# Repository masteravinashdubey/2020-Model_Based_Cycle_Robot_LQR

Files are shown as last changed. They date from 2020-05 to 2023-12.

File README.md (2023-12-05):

# Model Based Robot Designing

- This project is part of e-YSIP(E-yantra Summer Internship Programme), 2020.
- Project Mentors: Avinash Dubey, Avijit Pandey
- Project Interns: Shreya Rastogi, Jai Garg, Chinmay Palaye
- The objective of this project is to understand and implement LQR based robot modelling.
- In this Project, we'll learn to design control strategies & model various robots.
- We will simulate different systems and robots based on the chosen model.
- We will also be building learning modules and experiments for better understanding of topics.
- The project has been divided into weeks. The work done in each week is contained in that weeks folder.
- Daily reports folder contains daily reports till day 6 for the team. After that the interns updated their personal reports.
- Meeting reports folder contains the minutes of the meetings with the mentors.
- Project progress report folder tracks the progress of the project so far.
- Weekly reports folder contains the weekly reports.
- The video link is : <a href="https://www.youtube.com/watch?v=THvqfcC5Y-I&list=PLK0jpMYIBd6B1-mDQZwADi5OlnOiK6k9m&index=19"> LQR based Cycle Robot </a>

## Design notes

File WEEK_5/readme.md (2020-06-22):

# Optimal Control Strategy
We were supposed to design 4 experiments/explanatory documents for this week.
1. Defining LQR Control. Impact of Q and R matrix (LQR_CONTROL)
2. Implementing LQR Control in Octave (LQR_control_Octave)
3. Implementing the Feedback in Arduino. Tuning the Parameters. (sensors_and_tuning)
4. Strategy for Navigation Via Remote Control. Debugging the System.

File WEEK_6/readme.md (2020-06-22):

# Hardware Implementation of Cycle Bot

This folder contains all the codes which have been used in Cyclebot Implementation.
- cycle_bot_arduino : main code of the bot
- timerInterrupt : code for the two timers being used
- Cycle__bot.m : Octave code for K matrix calculation using dlqr()
- mpu caliberation.txt : offset calculation of mpu
- serialTest

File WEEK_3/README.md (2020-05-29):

# Robot Hardware
- 3 experiments to be designed.
  1. 3D Modelling in VREP.
  2. Collecting data using GY87 and filtering it, comparison between various filters.
  3. Interfacing XBee with Arduino.
- 2 videos to be made
  1. Factors to consider while choosing hardware
  2. Do's and Don'ts of robot hardware

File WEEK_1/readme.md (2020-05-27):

# Simulation of Cycle Bot
- This week's work was divided into 3 tasks.
  1. Task 1: simulation of a Reaction wheel balanced inverted pendulum on a hinge.
  2. Task 2: simulation of a Reaction wheel balanced inverted pendulum on a pivot.
  3. Task 3: simulation of a Cyclebot.

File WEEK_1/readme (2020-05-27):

Simulation of Cycle Bot
- This week's work was divided into 3 tasks.
- Task 1 was the simulation of a Reaction wheel balanced inverted pendulum on a hinge.
- Task 2 was the simulation of a Reaction wheel balanced inverted pendulum on a pivot.
- Task 3 was the simulation of Cyclebot.

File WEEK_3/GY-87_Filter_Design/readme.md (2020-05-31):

# GY-87_Filter_Design
- This folder contains the experiment files for the topic GY-87 and filter design.
- There is an experiment problem file.(Experiment.pdf)
- There is an experiment solution file.(Filter_design_answers.pdf)
- The .tex files for both are also present.
- The folder Experiment_Octave_Files consists of all the files for the octave part of this experiment.

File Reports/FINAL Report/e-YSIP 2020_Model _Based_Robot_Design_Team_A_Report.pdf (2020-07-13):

## eYSIP 2020

### Model Based Robot Design

### Project ID 17

### Chinmay Palaye Jai Garg Shreya Rastogi Avinash Dubey Avijit Pandey Duration of Internship: 08/05/2020 − 27/06/2020

2020, e-Yantra Publication

# Model Based Robot Design

## Abstract

A self-balancing bicycle robot based on the concept of an inverted pendulum is an unstable and nonlinear system. This system balances using a reaction wheel, also known as inertia wheel. Behaviour of this system is studied by deriving a mathematical model of the system using Euler Lagrange method. This model is used to balance the cycle robot using LQR control method. To apply LQR, system is first linearized about the equilibrium points using Jacobian method. This model was first simulated in the simulation software CoppeliaSim (VREP). A physical cycle robot was designed in Fusion360 software, manufactured, and balanced. Project Overview video (https://www.youtube.com/watch?v=MRSbph5AvGU&t=7s)

### Completion status

The project has been completed successfully. Learning Modules were created for various topics of Control systems and LQR controller. Cyclebot was simulated in CoppeliaSim and also implemented using hardware.

## 1.1 Hardware parts

- GY87 10DOF 3axis accelerometer, gyroscope, magnetometer: Datasheet
- XBee Module: Datasheet
- Arduino Mega2560: Datasheet
- L298 motor driver: Datasheet
- GS5515MG Servo Motor: Datasheet

1

1.2. SOFTWARE USED

## 1.2 Software used

- CoppeliaSim:

– Version 4.0.0

– Download Link (https://www.coppeliarobotics.com/downloads)

– User Manual (https://www.coppeliarobotics.com/helpFiles/)

- GNU Octave:

– version 5.1.0.0

– Download Link (https://www.gnu.org/software/octave/download.html)

– Installation Steps (https://wp.stolaf.edu/it/installing-gnu-octave-on-windows/)

- Fusion 360TM:

– Version 2.0.8156

– Download Link (https://www.autodesk.com/products/fusion-360/free-trial)

– Installation Steps (https://knowledge.autodesk.com/support/fusion-360/troubleshooting/caas/sfdcarticles/sfdcarticles/How-does-Fusion-360-get-installed.html)

- Arduino IDE:

– Version 1.8.39.0

– Download Link (https://www.arduino.cc/en/main/software)

– Installation Steps (https://www.tutorialspoint.com/arduino/arduino_installation.htm)

## 1.3 Assembly of hardware

Circuit diagram and Steps of assembly of hardware with pictures for each step.

### Circuit Diagram

Figure 1.1 shows the circuit diagram of Cycle Bot.

www.e-yantra.org | 2

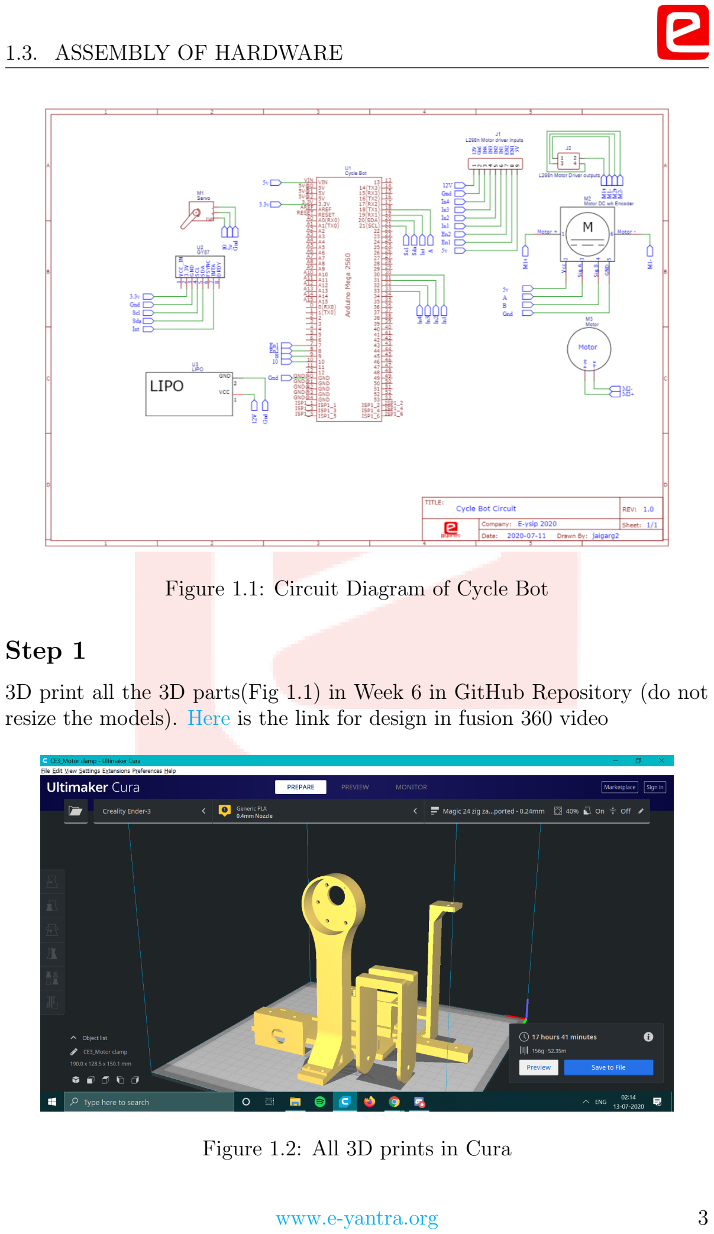
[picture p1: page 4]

1.3. ASSEMBLY OF HARDWARE

Figure 1.1: Circuit Diagram of Cycle Bot

### Step 1

3D print all the 3D parts(Fig 1.1) in Week 6 in GitHub Repository (do not resize the models). Here (https://www.youtube.com/watch?v=4ax1faUiTyk) is the link for design in fusion 360 video

Figure 1.2: All 3D prints in Cura

www.e-yantra.org | 3

1.3. ASSEMBLY OF HARDWARE

### Step 2

Attach Servo case and handle to the servo motor

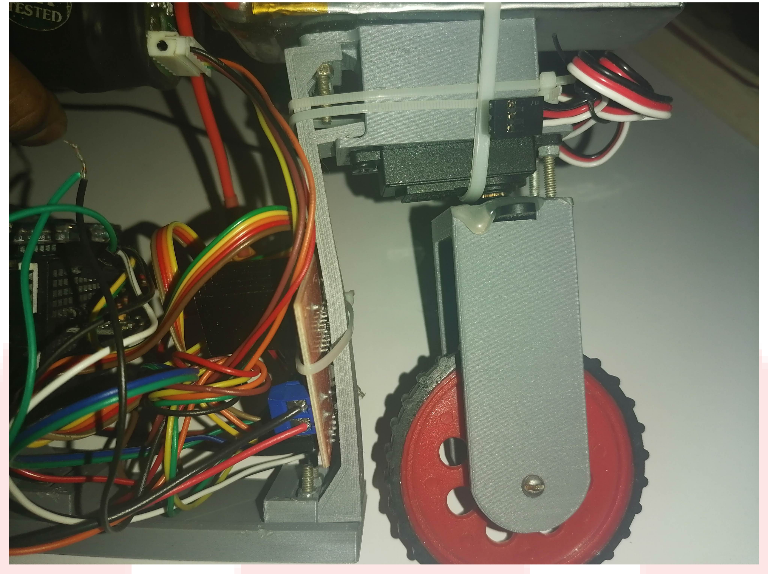
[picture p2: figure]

Figure 1.3: Front Assembly

### Step 3

Attach middle slab and base using screws.

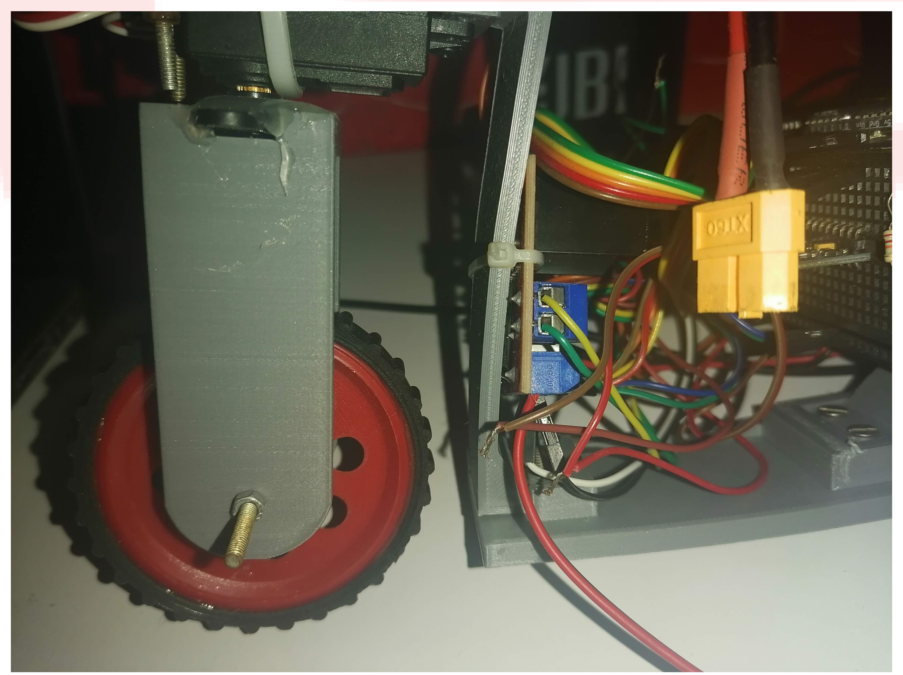
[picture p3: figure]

Figure 1.4: Base Connection

www.e-yantra.org | 4

1.3. ASSEMBLY OF HARDWARE

### Step 4

Connect reaction wheel motor and base motor to reaction wheel stand and motor clamp respectively and then attach both on the base using screws(Fix reaction wheel tightly).

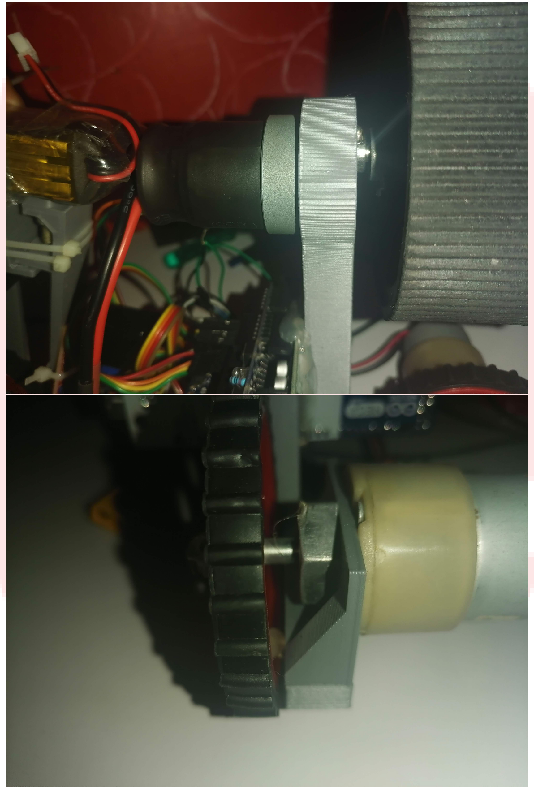
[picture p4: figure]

Figure 1.5: Reaction Wheel and Motor Clamp

www.e-yantra.org | 5

1.4. SOFTWARE AND CODE

### Step 5

Then Connect all the electronic Components according to the circuit diagram.

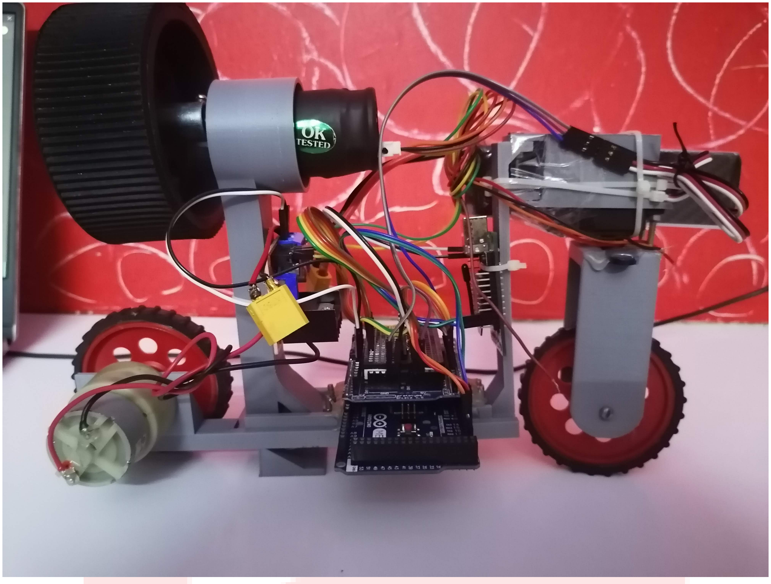
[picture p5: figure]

Figure 1.6: Fully assembled bot

## 1.4 Software and Code

GitHub link (https://github.com/masteravinashdubey/Model_Based_Robot_LQR/tree/master/WEEK_6) for the repository of code
Brief explanation of various parts of code:
- Main loop.ino: The main code where the rest of the header files and functions have been called.
- motor.h: The file where the functions and working of the motors and related calculations take place.
- controller lqr.h: The header file containing the controller of the system. The LQR controller has been implemented in this.
- DMP.h: This code gives the readings from the MPU6050 i.e. the roll and the pitch of the system.
www.e-yantra.org | 6

1.5. USE AND DEMO
- mpu.h: This code gives us the readings from the MPU6050 using filters.
- torque model.m: This is the octave code which fives us the value of the gain matrix i.e. K matrix for our system.
- xbee.h: This is for the communication between our bot and the remote via Zigbeee communication.

## 1.5 Use and Demo

Final Setup Image

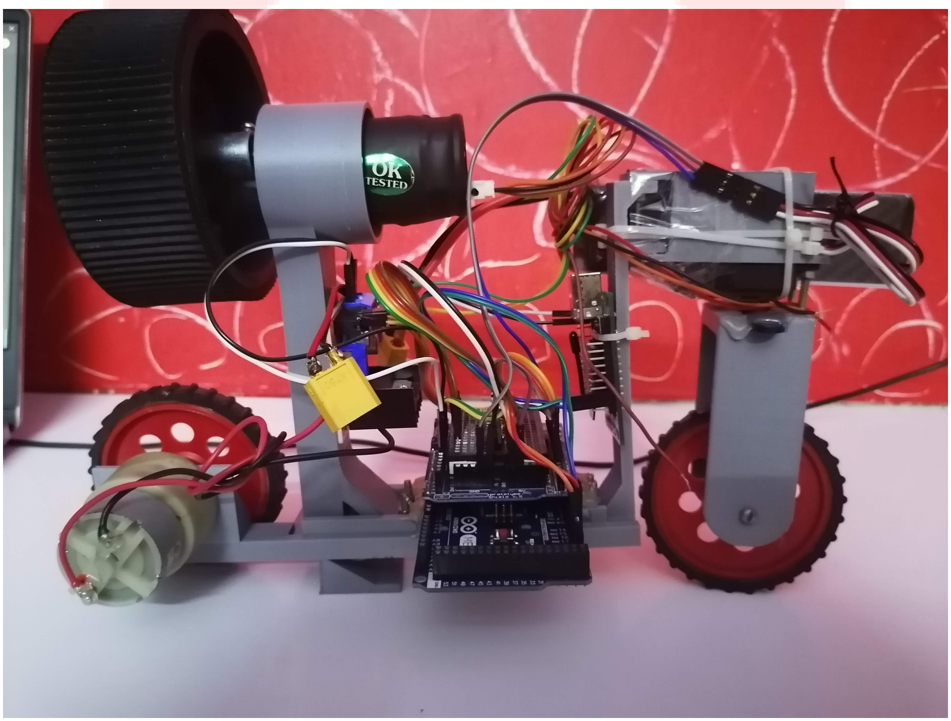
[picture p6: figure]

Figure 1.7: Fully assembled bot

Youtube Link (https://www.youtube.com/watch?v=o6guLBFLpi8) of demonstration video

## 1.6 Future Work

Presently we have managed to balance the cyclebot for a very short duration i.e. a few seconds. In the future the first thing to be implemented would be it’s successful balancing. Then more work can be done regarding it’s

www.e-yantra.org | 7

1.7. BUG REPORT AND CHALLENGES

movement. The cyclebot should be able to move forward, take turns, climb an inclined plane etc. in the future projects.

## 1.7 Bug report and Challenges

Failure or challenges faced during project:

- The hardware wasn’t available for making the cyclebot so we had to take help of a 3D printer.
- The implementation of LQR controller to balance the cyclebot was a huge challenge.
- Main challenge faced was in balancing the cyclebot.
- Usage of timers in the code was slightly tricky as well.
www.e-yantra.org | 8

# Bibliography

[1] Kiattisin Kanjanawanishkul, LQR and MPC controller design and comparison for a stationary self-balancing bicycle robot with a reaction wheel, 2015.
[2] Adam Owczarkowski, Dariusz Horla and Joanna Zietkiewicz, Introduction of feedback linearization to robust LQR and LQI control – Analysis of results from an unmanned bicycle robot with reaction wheel, 2019.
[3] Jepsen, Frank; Søborg, Anders; Pedersen, Anders R.; Yang, Zhenyu, Development and Control of an Inverted Pendulum Driven by a Reaction Wheel, 2009.
[4] Yon Yaw Lim, Choon Lih Hoo, and Yen Myan Felicia Wong, Stabilising an Inverted Pendulum with PID Controller, 2018.

9

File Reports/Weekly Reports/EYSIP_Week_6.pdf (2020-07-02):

# EYSIP 2020 Weekly Report

### Saturday, 21.06.2020

─

# Cycle BOT using LQR

## Team 1 (LQR)

Shreya Rastogi
Jai Garg
Chinmay Palaye

## Important Points

Hardware implementation of Cyclebot.

- cycle_bot_arduino : main code of the bot
- timerInterrupt : code for the two timers being used
- Cycle__bot.m : Octave code for K matrix calculation using dlqr()
- mpu caliberation.txt : offset calculation of mpu
- serialTest

## Relevant Links:

- All the work has been updated in the GitHub repository in the WEEK_6 folder.

Link (https://github.com/masteravinashdubey/Model_Based_Robot_LQR/tree/master/WEEK_6)

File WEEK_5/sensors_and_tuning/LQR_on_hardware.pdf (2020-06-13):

## Robot Design Robot Design using LQR

### Choice of Sensors and Tuning

### 1 Choice of Sensors:

The input given to the system, u = −Kx, depends on the gain matrix K, and the instantaneous values of all the state variables. Gain matrix can be calculated by using A and B matrices of the system, and setting appropriate values in Q and R matrices. On the actual robot, instantaneous values of all state variables are needed in order to calculate the input to the actuators. To get those values, various sensors are needed. Type of sensor depends on the type of value needed, and the structure of robot.

- Angular position of a joint: A rotary encoder can be used to get this. If angular velocity is needed, This value can be differentiated with respect to time using timer interrupts.

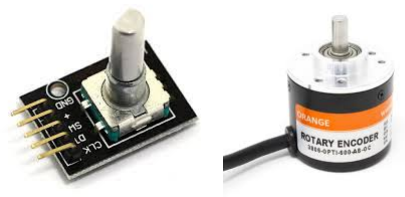
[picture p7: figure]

(a) (b)

Figure 1: Rotary Encoders

- Roll, pitch or yaw of a body: IMUs like accelerometer, magnetometer, etc. can be used. For rate of change, gyroscope can be used.

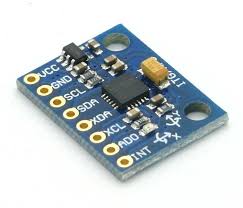
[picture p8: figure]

Figure 2: MPU6050: Accelerometer+Gyroscope

1

- Linear Position of joint: a linear encoder(e.g. LVDT) can be used. Some mechanism like rack and pinion can be used to make the use of rotary encoder to get the position. The differentiation technique can be used to get linear velocity as well.

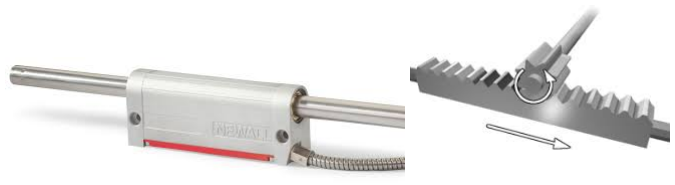
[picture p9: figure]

(a) Linear Encoder | (b) Rack and Pinion Mechanism

Figure 3: Linear Position Sensors

- Displacement of the robot: Rotary encoders can be attached to the robot with dummy wheels. Angular position of the encoder will be directly proportional to the displacement of robot. If walls are available for reference, distance sensors can be used to determine the distance for robot from the walls.

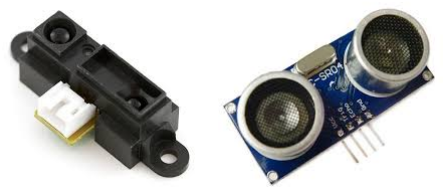
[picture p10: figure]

(a) Optical | (b) Sound based

Figure 4: Distance Sensors

Readings from all these sensors might have to be processed to match the units and conventions used while deriving the model.

2

### 2 Tuning of Q and R matrices:

To decide the gain matrix, Q and R matrices need to be adjusted such that the system is stable, and performance is optimal. Higher Q values mean that more preference is given to that state variable. When Q of some state variable is increased, gain values will change in such a way that the system will react more on change in the value of that variable. While tuning, observe the performance of the system and increase or decrease the weights accordingly.

3

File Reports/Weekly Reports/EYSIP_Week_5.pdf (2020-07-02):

# EYSIP 2020 Weekly Report

### Saturday, 13.06.2020

─

# Cycle BOT using LQR

## Team 1 (LQR)

Shreya Rastogi
Jai Garg
Chinmay Palaye

## Important Points

We designed 4 experiments/explanatory documents for this week.

1. Defining LQR Control. Impact of Q and R matrix.
2. Implementing LQR Control in Octave.
3. Implementing the Feedback in Arduino. Tuning the Parameters.
4. Strategy for Navigation Via Remote Control. Debugging the System.

## Relevant Links:

- All the work has been updated in the GitHub repository in the WEEK_5 folder.

Link (https://github.com/masteravinashdubey/Model_Based_Robot_LQR/tree/master/Week_5)

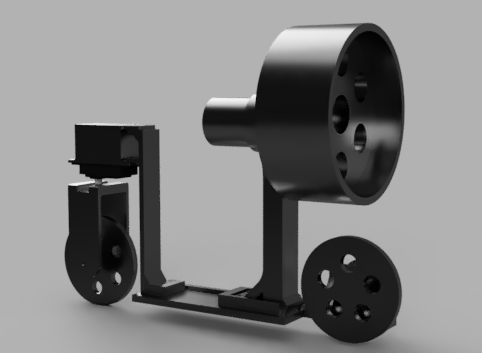
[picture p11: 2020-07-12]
WEEK_6/Bot design/Bot_3D_Design.png

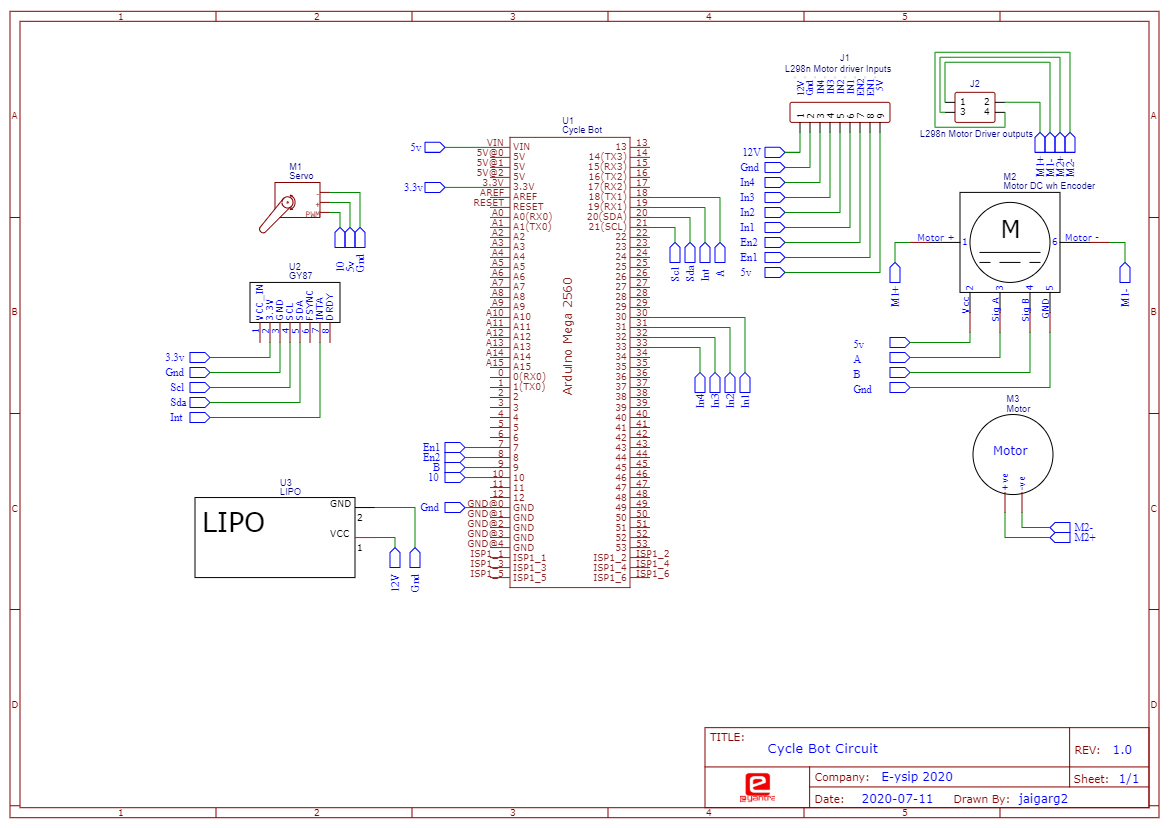
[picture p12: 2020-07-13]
WEEK_6/Schematic_E-YSIP 2020 Cycle Bot_2020-07-12_00-36-34.png

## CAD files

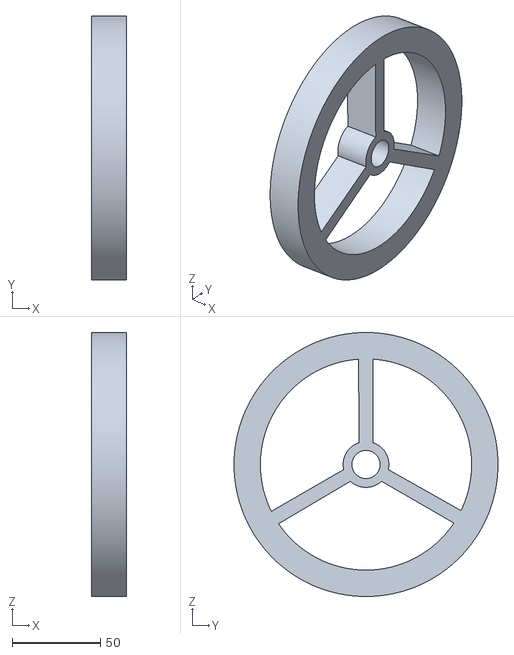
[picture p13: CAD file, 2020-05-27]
WEEK_1/Task_1/Fusion 360 files/Wheel.stl
20.0 x 150.0 x 150.0

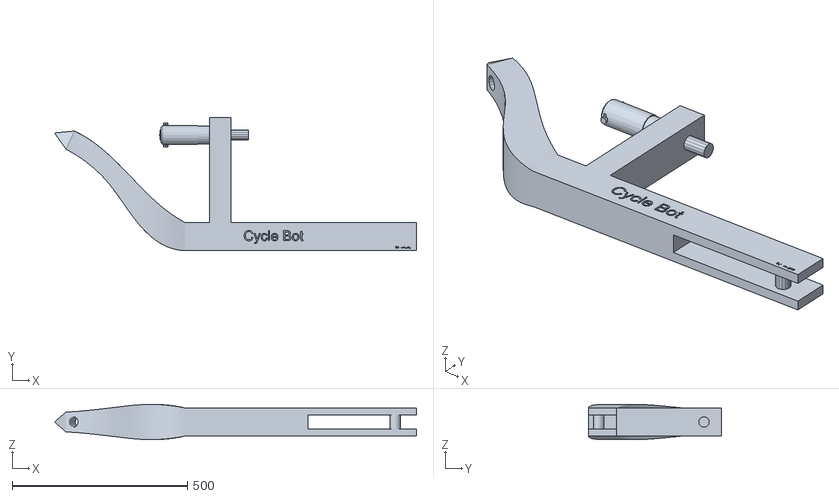
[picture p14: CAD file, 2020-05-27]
WEEK_1/Task_3/Design in Fusion 360/.stl_files/Cycle Body.stl
1032.6 x 380.0 x 100.1

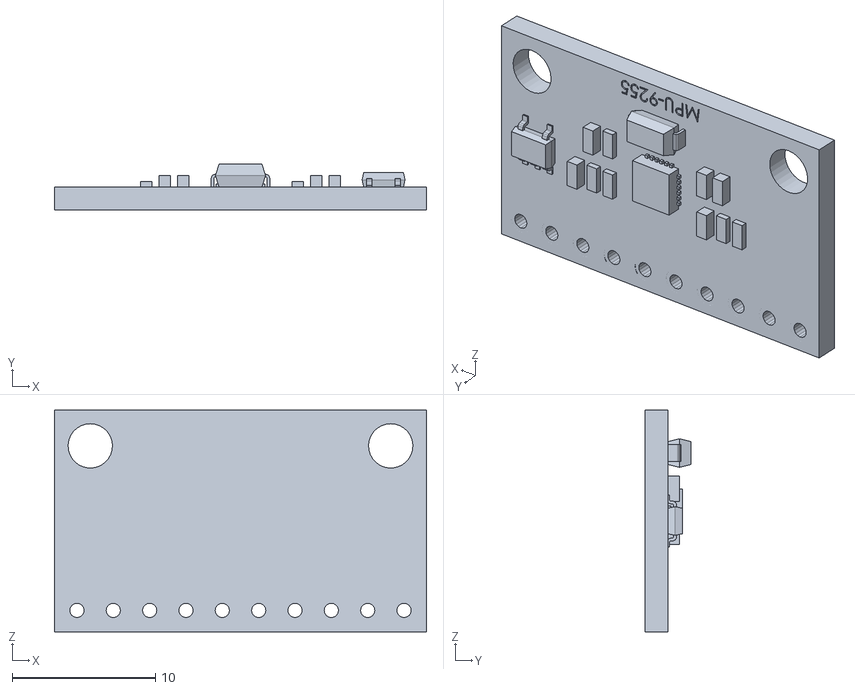
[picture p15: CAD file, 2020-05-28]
WEEK_3/Experiment 1/Fusion 360/Files/Gy-87.stl
26.0 x 3.20 x 15.5

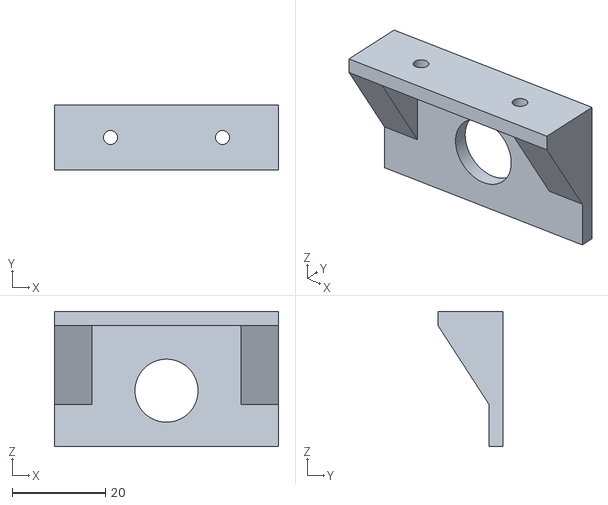
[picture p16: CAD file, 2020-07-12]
WEEK_6/Bot design/3D print Files/Motor clamp.stl
48.0 x 14.0 x 29.0

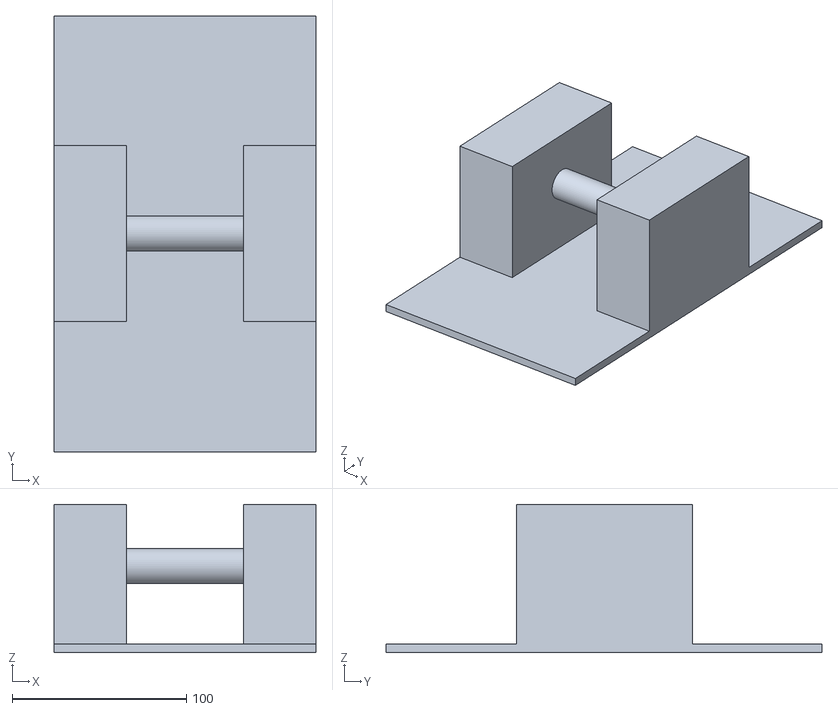
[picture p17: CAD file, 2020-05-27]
WEEK_1/Task_1/Fusion 360 files/Simple Base.stl
150.0 x 250.0 x 85.0

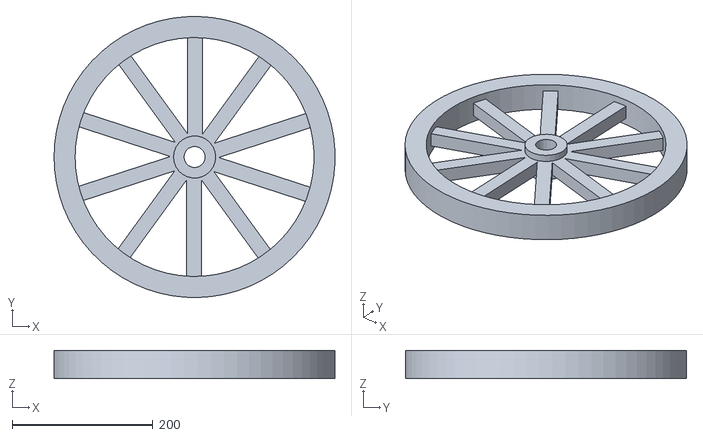
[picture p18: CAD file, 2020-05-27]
WEEK_1/Task_3/Design in Fusion 360/.stl_files/Wheel.stl
399.8 x 399.9 x 40.0

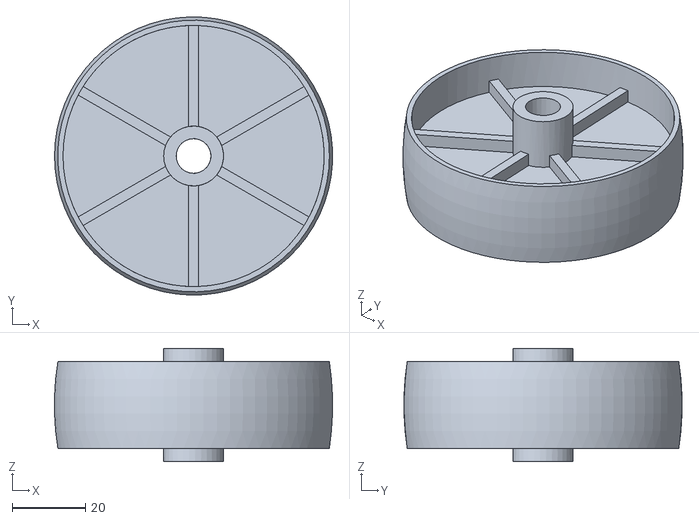
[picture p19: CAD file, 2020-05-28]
WEEK_3/Experiment 1/Fusion 360/Files/Wheel.stl
76.1 x 76.1 x 31.0

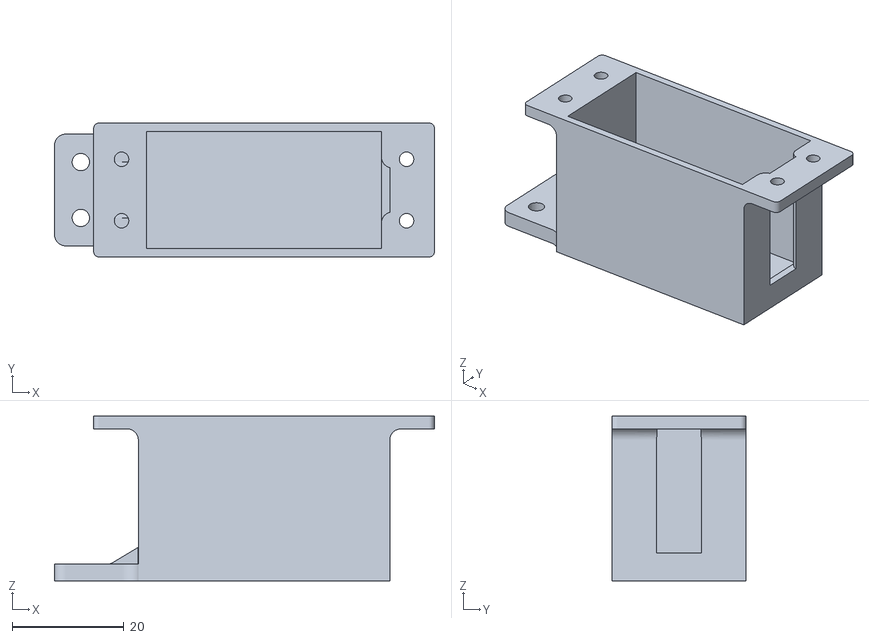
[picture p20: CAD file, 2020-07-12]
WEEK_6/Bot design/3D print Files/Servo case V2.stl
68.0 x 24.0 x 29.5

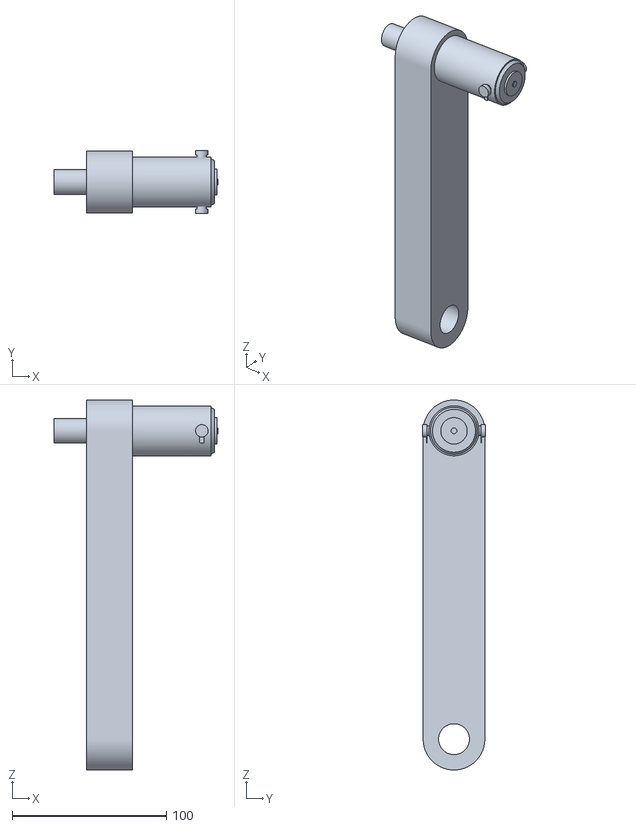
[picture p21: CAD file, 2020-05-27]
WEEK_1/Task_1/Fusion 360 files/Pendulum.stl
106.3 x 41.1 x 240.0

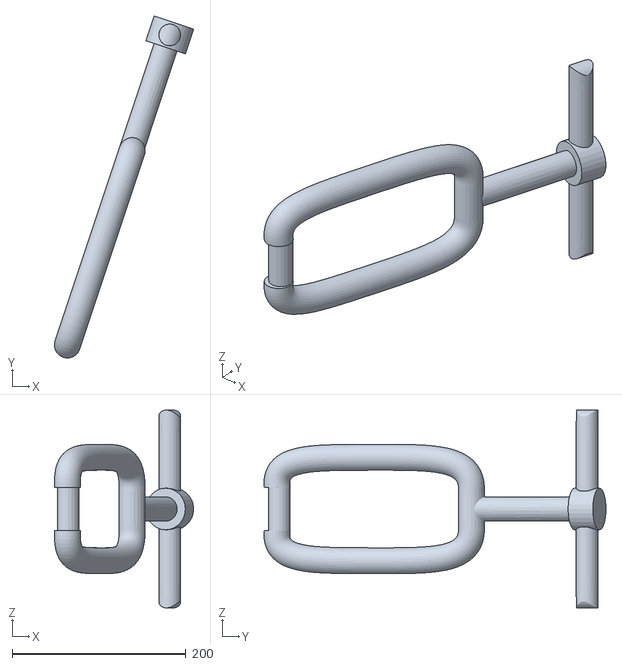
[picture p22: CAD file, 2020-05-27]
WEEK_1/Task_3/Design in Fusion 360/.stl_files/Handle.stl
160.4 x 394.1 x 228.0

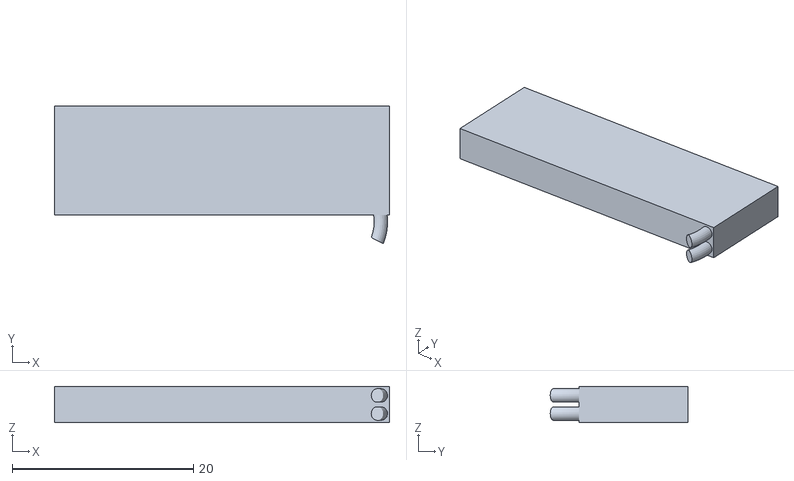
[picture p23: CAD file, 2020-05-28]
WEEK_3/Experiment 1/Fusion 360/Files/LiPo_Battery.stl
37.0 x 15.2 x 4.00

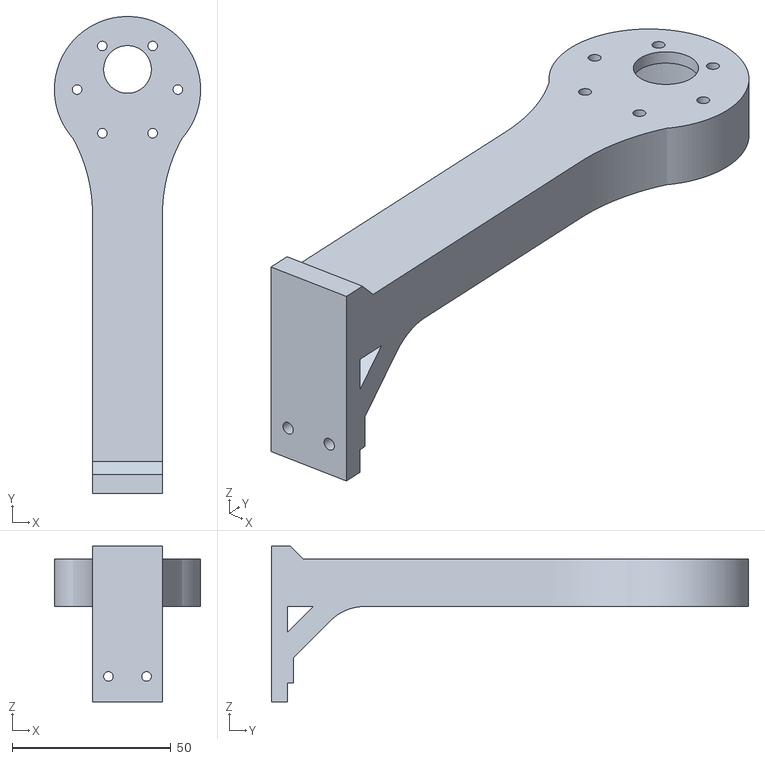
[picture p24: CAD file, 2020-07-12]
WEEK_6/Bot design/3D print Files/Reaction wheel v3.stl
46.0 x 150.1 x 49.0

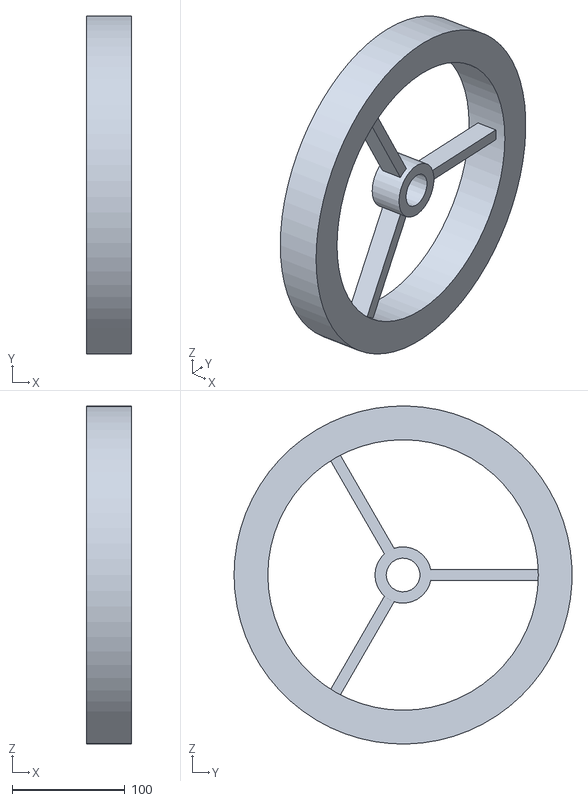
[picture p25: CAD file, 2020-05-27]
WEEK_1/Task_3/Design in Fusion 360/.stl_files/Reaction wheel.stl
40.0 x 299.8 x 299.9

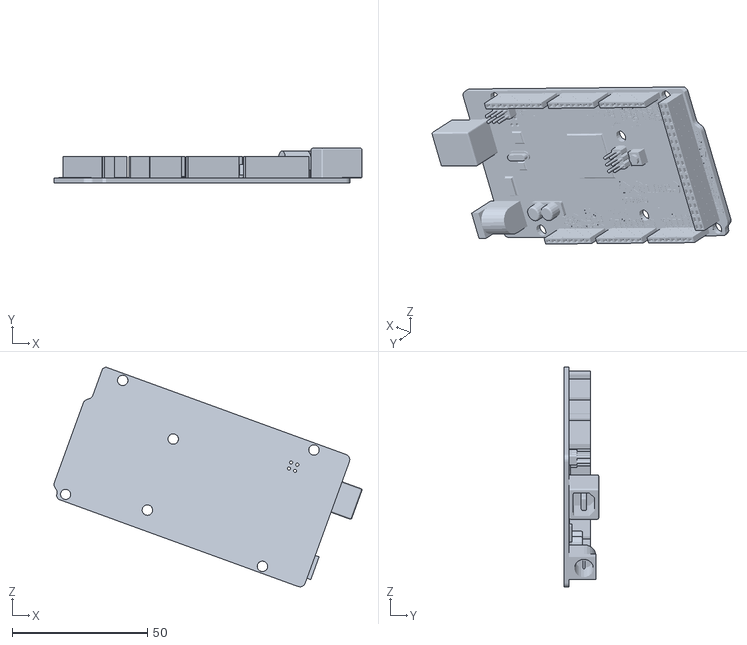
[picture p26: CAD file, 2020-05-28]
WEEK_3/Experiment 1/Fusion 360/Files/ARDUINO MEGA.stl
114.0 x 12.8 x 81.4

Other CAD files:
WEEK_6/Bot design/3D print Files/Middle slab.stl
WEEK_1/Task_3/Design in Fusion 360/.stl_files/Cycle Bot design v2.stl
WEEK_3/Experiment 1/Fusion 360/Files/Body.stl
WEEK_6/Bot design/3D print Files/Base V2.stl
WEEK_3/Experiment 1/Fusion 360/Files/DC Motor.stl
WEEK_3/Experiment 1/Fusion 360/Files/L298N Motor Driver.stl
WEEK_3/Experiment 1/Fusion 360/Files/Motor Clamp.stl
WEEK_3/Experiment 1/Fusion 360/Files/XBee.stl
WEEK_6/Bot design/3D print Files/Servo Steering for cycle bot v1.stl

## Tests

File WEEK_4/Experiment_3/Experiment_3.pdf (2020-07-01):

E-Yantra Summer Internship

PID:17 | 26th June, 2020

# State-Space Model and Controllability

### 1 Aim

Finding out the Parametric State-Space Model. Substituting practical values and checking for

controllability of the system.

### 2 Problem

- Consider the system of a Cyclebot. In the previous experiment we derived the state space

model of the system. The input to this system was an input torque. Find the model in

terms of an input voltage i.e. find the relation between voltage and torque and find the

resultant model of the system.

- The hardware or the cyclebot that you have built. Find it’s values, for example mass,

moment of inertia, torque etc. Substituting these values in the A and B matrices, check

whether the actual system is controllabale or not.

### 3 Solution

Let [θ, ˙θ, φ, φ˙
]

T be the state variables of the system

where:

θ: deflection of the pendulum from the vertical ˙θ: angular velocity of the pendulum

φ: angle of the reaction wheel
φ˙
: angular velocity of the reaction wheel

∴ State Space Representation of the system

x˙ = Ax + Bu | (1)

˙θ

¨θ

φ˙

φ¨

=

0 1 0 0

b
a

0 0 0

0 0 0 1
−

b
a

0 0 0

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
(a+I2)
aI2

Tr

where

a = (m1L

2
1 + m2L

2
2 + I1) | (2)
b = (m1L1 + m2L2)g | (3)

To control the speed of the reaction wheel to the desired one, the following mathematical model

is the physical behavior of the motor with a gear system:

V = Lm

di
dt + Rmi + Keωm

Tm = Kti

Tr = NgTm

where:

- V : motor supply voltage
- Ke : motor back emf constant
- ωm : motor angular speed
- Lm : armature coil inductance
- Rm : armature coil resistance
- i : armature current
- Tm : motor generated torque
- Kt

: motor torque constant

- Ng : gear ratio

The term of inductance can be neglected since, in general, the motor inductance value is much less than the motor resistance value (Lm«Rm). By using the relationship between the motor and the reaction wheel, i. e., φ˙ = ωr, ωm = Ngωr, where ωr is reaction wheel angular speed, the

motor supply voltage can be found in terms of the reaction wheel angle as follows:

Tr = NgKt

V − KeNgφ˙

Rm

The Model:

˙θ

¨θ

φ˙

φ¨

=

0 | 1 0 | 0
a21 | 0 0 a24
0 | 0 0 | 1
a41 | 0 0 a44

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
where:

a21 =

b
a

, a24 =

KtKeNg

2
aRm

, a41 = −

b
a

, a44 = −

(a+I2)
aI2

KtKeNg

2
Rm

, b2 = −

KtNg
aRm

, b4 =

(a+I2)
aI2

KtNg
Rm

### Parameters of Our Cyclebot

Parameters | Values
Distance from pivot to COM of Body (L1) | 76.83mm
Distance from pivot to COM of Reaction Wheel (L2) | 148.53mm
Mass of Bicycle (M1) | 763g
Mass of Reaction Wheel (M2) | 357g
MOI of Body about COM (I1) | 2.1x10⁶ gmm²
MOI of Reaction wheel about COM (I2) | 8.2x10⁵ gmm²
Motor Resistance (Rm) | 13.3 Ω
Motor Torque Constant (Kt) | 2.77x10⁻²Nm/A
Motor Back EMF Constant (Ke) | 1.27x10⁻²V s/rad
Motor gear ratio (Ng) | 1:30

The model obtained by substituting these values is:

˙θ

¨θ

φ˙

φ¨

=

0 | 1 0 | 0
75.64 | 0 0 | 1.6482
0 | 0 0 | 1

−75.64 0 0 −2.0678e − 05

θ
˙θ

φ
φ˙

+

0

−4.3151

0

80.512

V

Using the above A and B matrices and the controllability matrix of the system

CO = [B, AB, A²B, A³B]

we check whether this system is controllable or not. Using the ctrb(A,B) function in octave,

we find the controllability matrix of this system. Then using the rank(CO) function we get

rank = 4, which proves that this system is controllable.

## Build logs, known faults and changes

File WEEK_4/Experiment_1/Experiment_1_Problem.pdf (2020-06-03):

E-Yantra Summer Internship

PID:17 | 3rd May, 2020

# Kinetic and Potential energy of a system

### 1 Aim

To find out the Kinetic energy and Potential energy of a system. Using these two quantities,

find out the Lagrangian of the system and the Euler Lagrange equation.

### 2 Problem

Consider the system of a Cyclebot. A Cyclebot is a robot having two wheels and balanced by

the help of a reaction wheel. It resembles a self balancing bot system. For this system, find out

the Kinetic energy,the Potential energy and then subsequently go on to find it’s Lagrangian and

the Euler Lagrange equation.

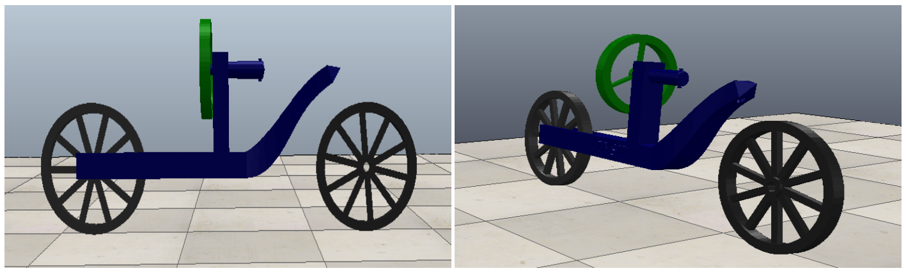
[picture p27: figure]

List of symbols:

- m1 : mass of pendulum
- L1 : Distance between pivot and COM of pendulum
- I1 : Moment of inertia of pendulum about it’s COM
- m2 : mass of reaction wheel
- L2 : Distance between pivot and COM of reaction wheel
- I2 : Moment of inertia of reaction wheel about it’s COM
- θ, ˙θ: Tilt angle and angular velocity of bicycle
- φ, φ˙
: Angular position and angular velocity of reaction wheel
- Tr : Torque provided to the reaction wheel

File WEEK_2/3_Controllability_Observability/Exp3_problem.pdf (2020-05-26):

### E-Yantra Summer Internship

PID:17/Shreya Rastogi | May 2020

# Controllability and Observability

## 1 Problem Statement

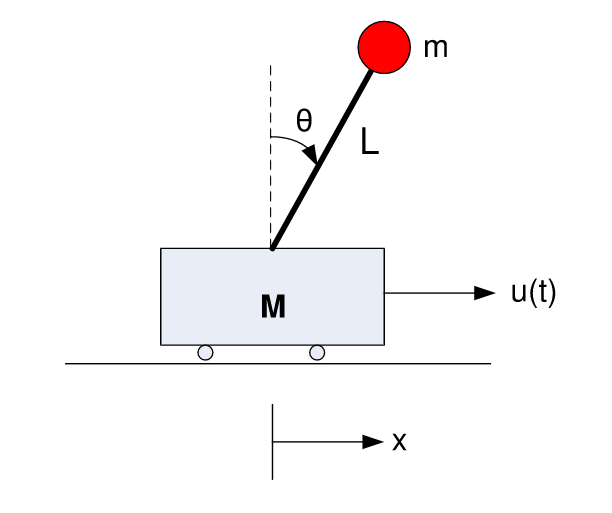
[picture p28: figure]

Consider a Cart Pendulum system. It is a horizontally moving cart with an inverted pendulum

attached to it on the top. The following is the state space representation of the system:

State Equation:

x˙ =

0 1 | 0 | 0

0 0 −1.96 0

0 0 | 0 | 1
0 0 | 5.88 | 0

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
−0.1

V

Output Equation:

Y =

1 0 0 0

0 1 0 0

0 0 1 0

0 0 0 1

So, as you can see the A, B and C matrices of the system have been provided to you. Comment

on whether the given system is controllable and or observable. You need to support your answer

with a proof for your explanation.

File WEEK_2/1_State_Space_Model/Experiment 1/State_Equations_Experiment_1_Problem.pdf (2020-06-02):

EYSIP 2020
PROJECT 17

EYSIP 2020
PROJECT 17

EYSIP 2020
PROJECT 17

## State Space Equation (Problems)

by

### Jai Garg

EYSIP 2020 –

Page 2

## 1 Spring Mass System

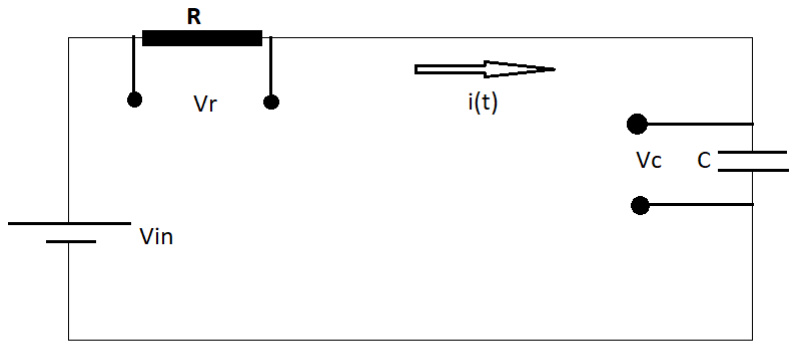
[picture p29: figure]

Figure 1: RC Circuit

Consider a RC circuit where input voltage is V in and current through the circuit is i(t), value of resistor is R and capacitor C is connected to the resistor in series,Voltage across resistor is Vr and voltage across capacitor is Vc.
Find out state the state variables for system and also derive the state space model using those state variables of this system.

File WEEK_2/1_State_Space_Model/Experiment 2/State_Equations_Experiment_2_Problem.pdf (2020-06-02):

EYSIP 2020
PROJECT 17

EYSIP 2020
PROJECT 17

EYSIP 2020
PROJECT 17

## State Space Equation (Problem)

by

### Jai Garg

EYSIP 2020 –

Page 2

## 1 Inverted Cart Pendulum

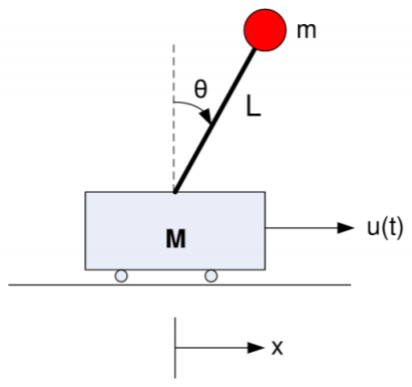
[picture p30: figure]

Figure 1: Inverted Cart Pendulum

Consider a Cart Pendulum system. It is a horizontally moving cart with an inverted pendulum attached to it on the top. Here a inverted pendulum is pivoted to cart of mass M and input force to the cart is u(t),where mass of the pendulum bob is m will length L, if the pendulum make a angle θ with the vertical then find out the state variables for the system and them derive the state space equations and output equations of this system.

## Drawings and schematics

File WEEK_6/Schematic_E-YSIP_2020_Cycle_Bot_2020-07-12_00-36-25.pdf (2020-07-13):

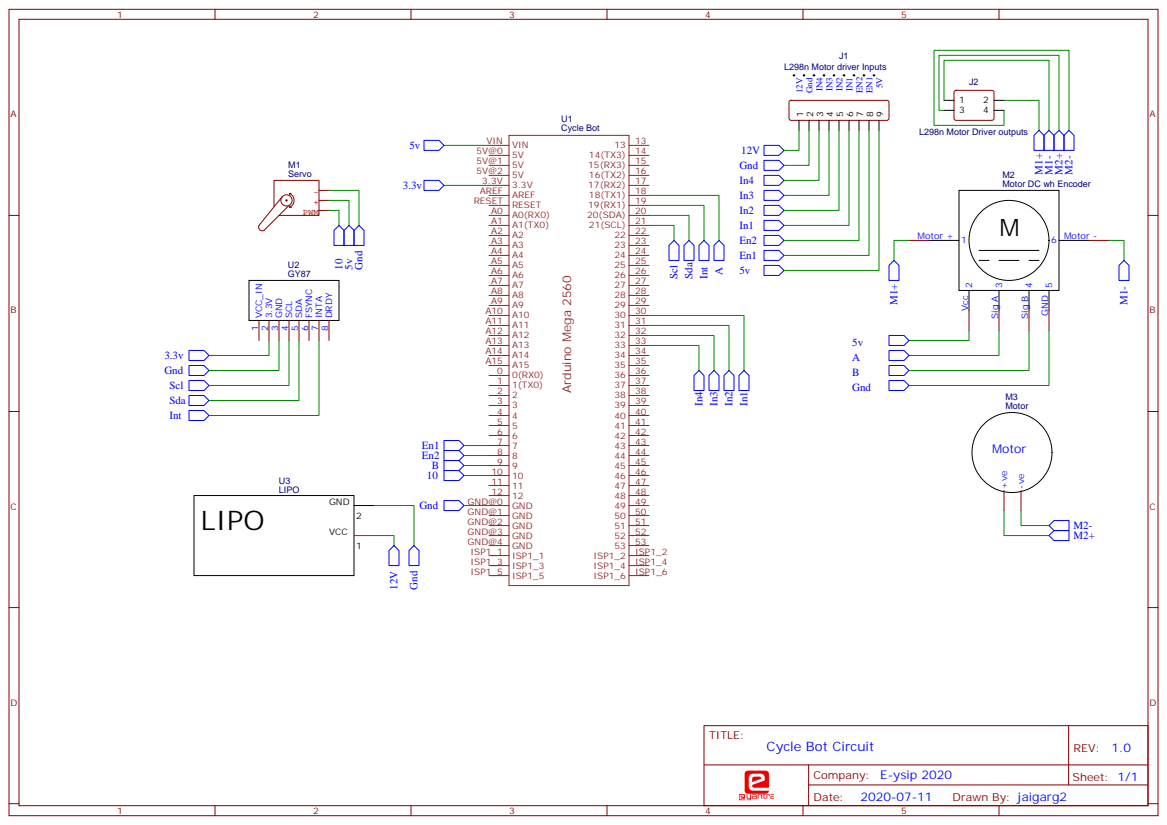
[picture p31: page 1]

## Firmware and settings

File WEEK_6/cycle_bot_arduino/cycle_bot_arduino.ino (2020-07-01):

#define F_CPU 16000000
#include "I2Cdev.h"
//#include "MPU6050.h"
#include<Arduino.h>
#include "MPU6050_6Axis_MotionApps20.h"
#include "Wire.h"
#include"DMP.h"
#include"xbee.h"
#include"motor.h"
#include"mpu.h"

#include<Servo.h>
#define PI 3.14159
#define encPin1 18     //SET PIN NUMBERS
#define encPin2 19
#define servoPin 9

//XBee mod(&Serial1);  	//mention the name of serial being used to communicate with XBee
motor reaction(31, 30, 7); //change the pin numbers here
motor drive(32, 33, 8);   //change the pin numbers here
#include"controller_lqr.h"
Servo handle;
//CompFil mpu6050;
volatile int encoderCount = 0, prevCount = 0;
float previousRoll=0,angVelocity=0;
long prevtime = 0;

char sampleTime(long Time)
{
  return (Time * 16000 / 1024);
}
void setup()
{

#if I2CDEV_IMPLEMENTATION == I2CDEV_ARDUINO_WIRE
  Wire.begin();
#elif I2CDEV_IMPLEMENTATION == I2CDEV_BUILTIN_FASTWIRE
  Fastwire::setup(400, true);
#endif

  Serial.begin(115200);

//  mpu6050.init();
MPUInit();
  Serial.println("going in loop");
  handle.attach(servoPin);
  handle.write(0);
  pinMode(encPin2, INPUT_PULLUP);
  pinMode(encPin1, INPUT_PULLUP);
  attachInterrupt(digitalPinToInterrupt(encPin1), encoderHandler, RISING);

  enable_timer();


  Serial.println("ok");

}
bool check = 0, check2 = 0;


void loop()
{
  //Serial.println(check);
  //Serial.println(mpu.roll_deg);
  //  Serial.print("\t");
  //Serial.println(mpu.roll);
  //  Serial.print("Omega:\t");
  //  Serial.println(mpu.omega);
//
//  if ((micros() - prevtime) >= 5000)
//  {
//    //  Serial.println("going in lqr");
//// lqr(ypr[2],angVelocity, phi, phidot);
//
//    prevtime = micros();
//  }
getDMP();
  if (check2)
  {
//    mpu6050.read_accel();
//    mpu6050.read_gyro();
//    mpu6050.complimentary_filter_roll();
    // Serial.println(mpu.roll_deg);
       check = 0;
    angVelocity=(ypr[2]-previousRoll)/0.005;
    previousRoll=ypr[2];
 lqr(ypr[2],angVelocity, phi, phidot);
    
  }
  if (check)
  {
        check2 = 0; 
    phidot = (encoderCount - prevCount) * 2 * PI / (270 * 0.01); //in rad/sec
    prevCount = encoderCount;
    //Serial.println(phidot);
  
  }
}

void encoderHandler()
{
  if (digitalRead(encPin2))
    encoderCount++;
  else
    encoderCount--;

  phi = encoderCount * 2 * PI / 270;
//  Serial.println(encoderCount);
//  if(phi>360)
//  encoderCount=0;
}

void enable_timer()
{
  noInterrupts();          // disable all interrupts

  TCCR2A = (1 << WGM21);   //CTC mode
  TCCR2B = 7;              //1024 prescaler
  OCR2A = sampleTime(5);             // compare match register, setting for 10ms
  TIMSK2 = (1 << OCIE2A);  // enable timer compare interrupt
  TCNT2  = 0;

  TCCR0A = (1 << WGM01);          //CTC mode
  TCCR0B = (1 << CS02) | (1 << CS00); //1024 prescaler
  OCR0A = sampleTime(3);                     // compare match register, setting for 3ms
  TIMSK0 = (1 << OCIE0A);         // enable timer compare interrupt
  TCNT0  = 0;

  interrupts();             // enable all interrupts
}
ISR(TIMER2_COMPA_vect)
{
  check2 = 1;
//Serial.println("ok");

  //  PORTJ^=0x01;
}

ISR(TIMER0_COMPA_vect)
{
  check = 1;
  //  PORTJ^=0x02;
}

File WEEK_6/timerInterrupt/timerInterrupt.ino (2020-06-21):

#include <avr/io.h>
#include <avr/interrupt.h>
#include<Servo.h>

void enable_timer()
{
  noInterrupts();          // disable all interrupts
  
  TCCR2A = (1<<WGM21);     //CTC mode
  TCCR2B = 7;              //1024 prescaler
  OCR2A = 156;             // compare match register, setting for 10ms
  TIMSK2 = (1 << OCIE2A);  // enable timer compare interrupt
  TCNT2  = 0;

  TCCR0A = (1<<WGM01);            //CTC mode
  TCCR0B = (1<<CS02)|(1<<CS00);   //1024 prescaler
  OCR0A = 46;                     // compare match register, setting for 3ms
  TIMSK0 = (1 << OCIE0A);         // enable timer compare interrupt
  TCNT0  = 0;
  
  interrupts();             // enable all interrupts
}

Servo handle;
bool s0=1,s2=1;
int main(void)
{
  enable_timer();
  handle.attach(8);
//  DDRJ=255;
  pinMode(14,1);
  pinMode(15,1);
    /* Replace with your application code */
    while (1) 
    {
      for(int i=0;i<90;i++)
      {
        handle.write(i);
        delay(50);
      }
      for(int i=90;i>0;i--)
      {
        handle.write(i);
        delay(50);
      }
    }
}

ISR(TIMER2_COMPA_vect)
{
  if(s2)
  {
    digitalWrite(15,1);
    s2=0;
  }
  else
  {
    digitalWrite(15,0);
    s2=1;
  }
  //  PORTJ^=0x01;
}

ISR(TIMER0_COMPA_vect)
{
  if(s0)
  {
    digitalWrite(14,1);
    s0=0;
  }
  else
  {
    digitalWrite(14,0);
    s0=1;
  }
//  PORTJ^=0x02;
}

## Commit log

2020-05-27 Organised Repo
    Organised Repo
    [Cycle Body.stl, Cycle Bot design v2.stl, Handle.stl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]
2020-05-28 commit on 'master'
    [Cycle Body.stl, Cycle Bot design v2.stl, Handle.stl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]
2020-05-28 Added Fusion 360 files
    [ARDUINO MEGA.stl, Body.stl, DC Motor.stl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]
2020-05-29 Create Gy-87 Sample Data Set.csv
    [Gy-87 Sample Data Set.csv]
2020-05-29 Added GY-87 Sample Data
    [Gy-87 Sample Data Set.csv]
2020-05-29 Rename Gy-87 Sample Data Set.csv to data.csv
    [data.csv]
2020-06-04 Create Servo Steering Part Test 2.mp4
2020-06-13 added count encoder pulses, measure RPM
2020-06-21 timer Interrupt testing
2020-06-24 Revert "update"
    This reverts commit 79367d2087d70c8369f24c75a27f991d03c9bafb.
    [controller_lqr.h, cycle_bot_arduino.ino]
2020-07-02 timer lib added
2020-07-02 torque model
2020-07-12 Fully updated
    [Base V2.stl, Middle slab.stl, Motor clamp.stl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]
2020-07-13 Create Schematic_E-YSIP 2020 Cycle Bot_2020-07-12_00-36-34.png
